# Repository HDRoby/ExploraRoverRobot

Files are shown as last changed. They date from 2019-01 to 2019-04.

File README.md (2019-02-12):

# Explora Rover Robot
6 wheels drive, all terrain, autonomous robot designed as a platform to experiment with autonomous driving vehicle.

Explora Robot is based on a well known commercial chassis widely available for hobbists 
[Dagu Thumper 6WD](https://www.sparkfun.com/products/11056).

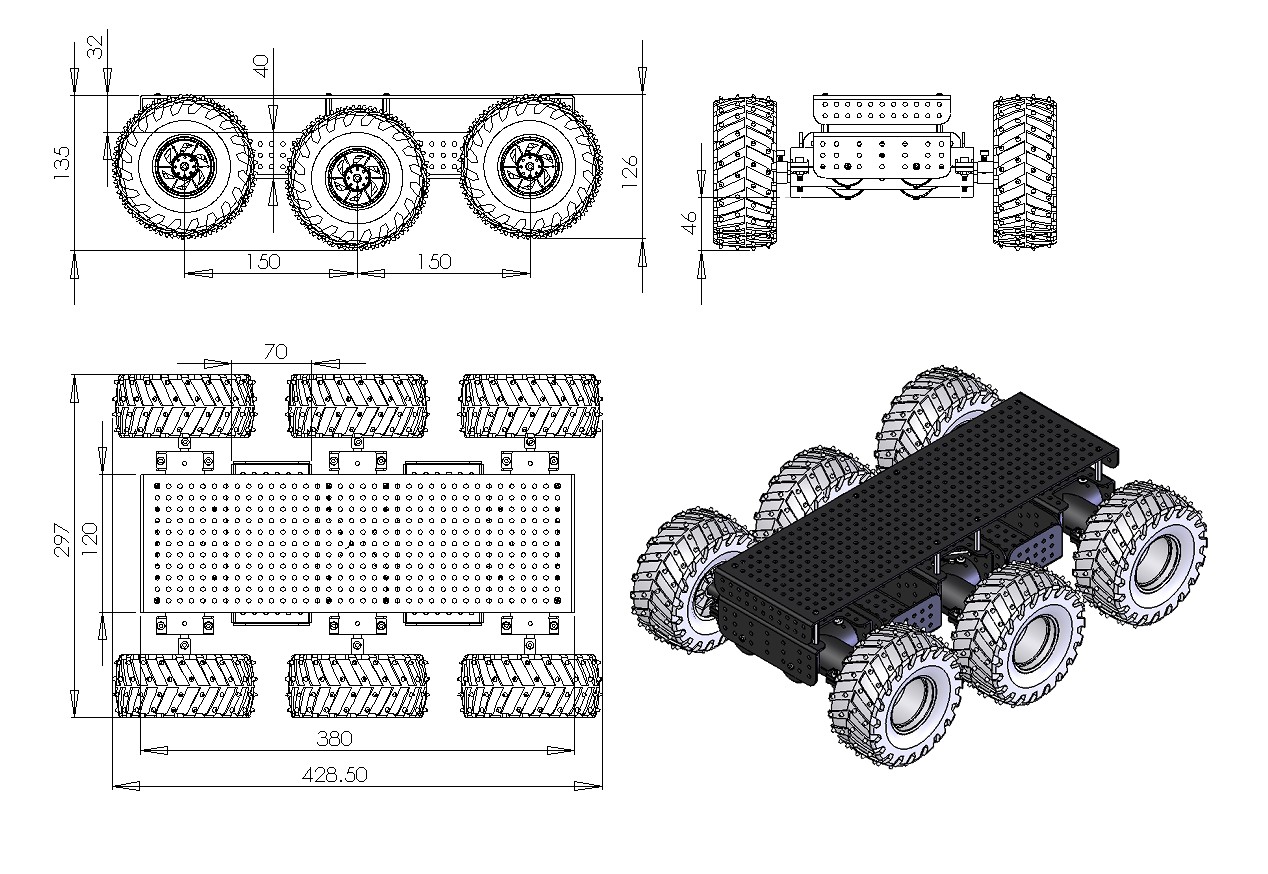
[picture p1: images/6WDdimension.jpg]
Dagu Thumper 6WD


Aim of this project is to design and build a robotic platform that will provide a set of interfaces, both software and hardware, that allow to build new layers with extended functionalities. Initial capabilities will include:

- indoor and outdoor navigation
- remote control and monitoring
- obstacle detection and avoidance
- simultaneus location and mapping (SLAM)
- viewpoints and landmark navigation
- terrain traversability estimation
- terrain negotiation
- path planning
- energy management and harvesting
- center of mass and pose estimation

## Tenets

- The system is open for modification without major disruption in all the parts.
- The robot can operate outdoor but its not designed for harsh environment. i.e. wet or dirty surfaces are allowed while waterproof is not in the scope.
- The energy consumption is frugal and a certain degree of autonomy is pursued. i.e. solar panel for energy harvesting or self recharging station could be implemented.
- The communication is bi-directional and mainly intended for monitoring and configuration than control (RC style).
- The robot can take advantage of many and concurrent localisation systems to establish its position in the environment. i.e. GPS, vision, LIDAR, utrasound, odometry, IMU, ...

## High level systems

Systems

### Power management system

This is responsible for providing power to the rover and all its subsystems, to monitor and recharge the batteries using both an external power source and solar panels. The system monitors the current drawn in real time by its major components: motors and all sub-systems; where possible each sub-system will provide its own power consumpion. Communications with the microcontroller (Arduino Micro) and other sub-systems is achieved via UART for the physical layer and with MQTT broker at ISO Application Layer (there will be a process on the main board (Raspberry Pi) that will have a process that act as a MQTT broker and that can communicate with a UART). 

Two mechanichal switches isolate the batteries from the rest of the system.

Power management system

### Motion control system

Motion control system

### Communication system

Communication system

### Logging system

The logging system is responsible for collecting data from each subsystem and storing it locally; the database of choice is InfluxDB (https://www.influxdata.com/time-series-platform/influxdb) that is a high-performance data store written specifically for time series data. The data we want lo log is in the format of time series and can be grouped in:
- **instrumentation data**. This is the data collected by the log system for each process that runs on every Raspberry PI. We use a logger that persists data on files, organised in folders with a specific naming convention (details in the paragraph). InfluxDB is installed on the main RPI and each other RPI has a process that periodically reads and import the log files into the DB, grouped by severity and by source and that takes care of their housekeeping.
- **system health data**. This collects all the data that allows to monitor and understand the system status. i.e. wifi RSSI, 2.4GHZ radio status, battery levels, system uptime, solar panes in use, number of remote sessions, number of battery recharges since day 1, etc.
- **sensors data**. This is the main source of data and is a collection of all the sensors, logged at the most appropriate rate. The only thing is not logged here, and probably is only stored in a folder, is the image video and audio (when capture is on) and image stills.

To complement the logging system, we will use Grafana  (https://grafana.com) to plot the data series collected.

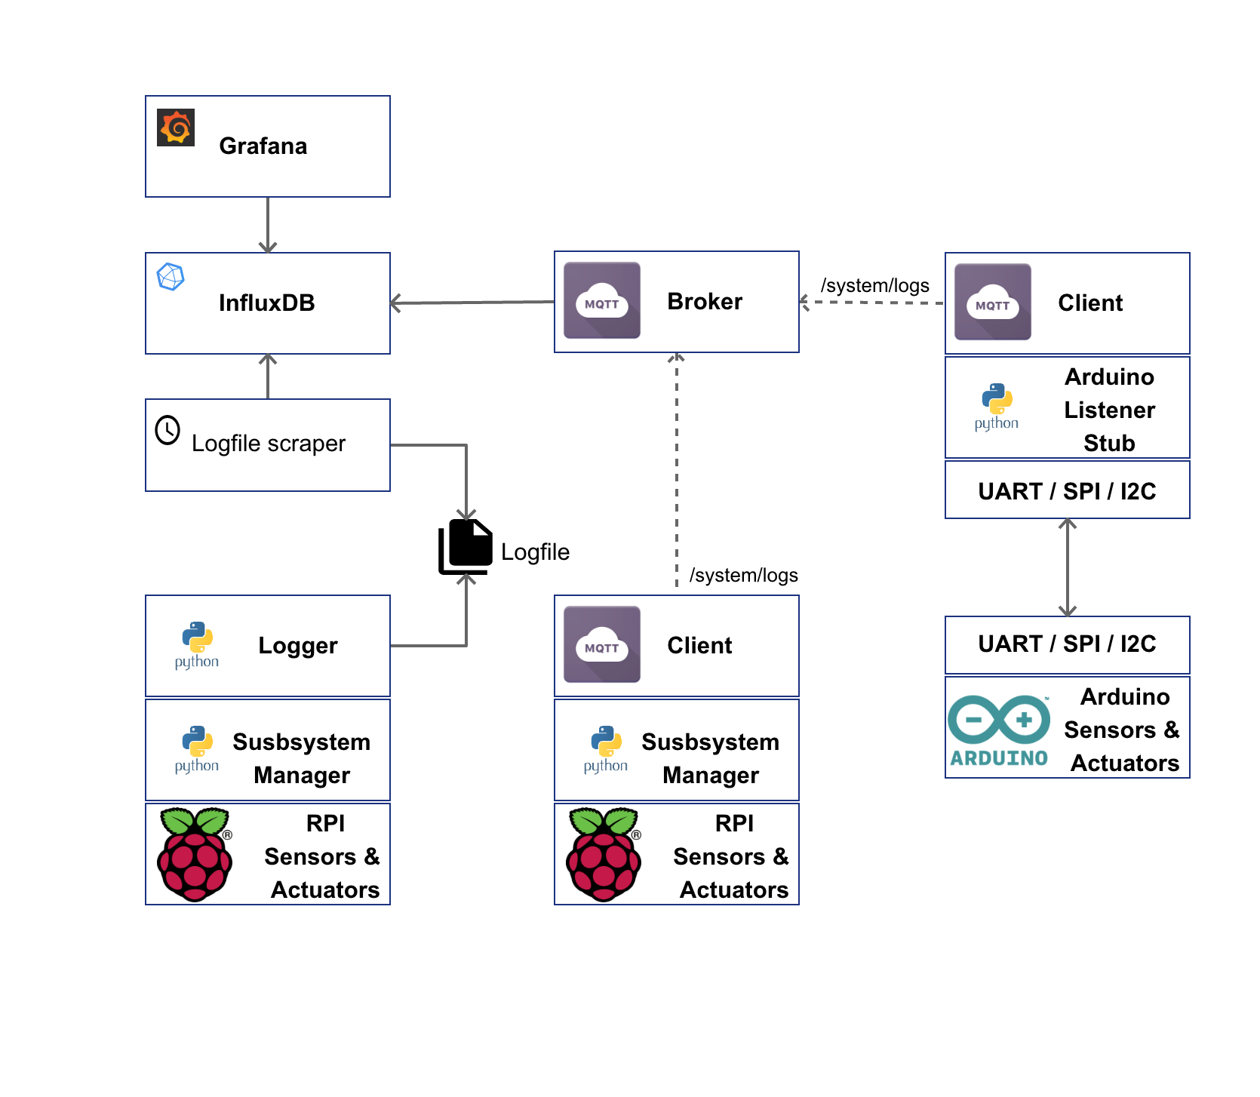
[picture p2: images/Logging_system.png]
Logging system


### Raspberry PI and Arduino systems
RPI is a much more powerful board than Arduino and the Linux OS simplify the management of the overall system, from the inter process communication (IPC) to the filesystem, wireless connectivity (WIFI & BTLE), multi process and multi threading. This is an overview of the architecture used to interact among a RPI and one or more Arduino. Note: in the robot there will be more than a single unit like this, that we consider as a basic processing unit (RPI + 1 or 2 Arduino) all RPIs are connected via Ethernet hub.

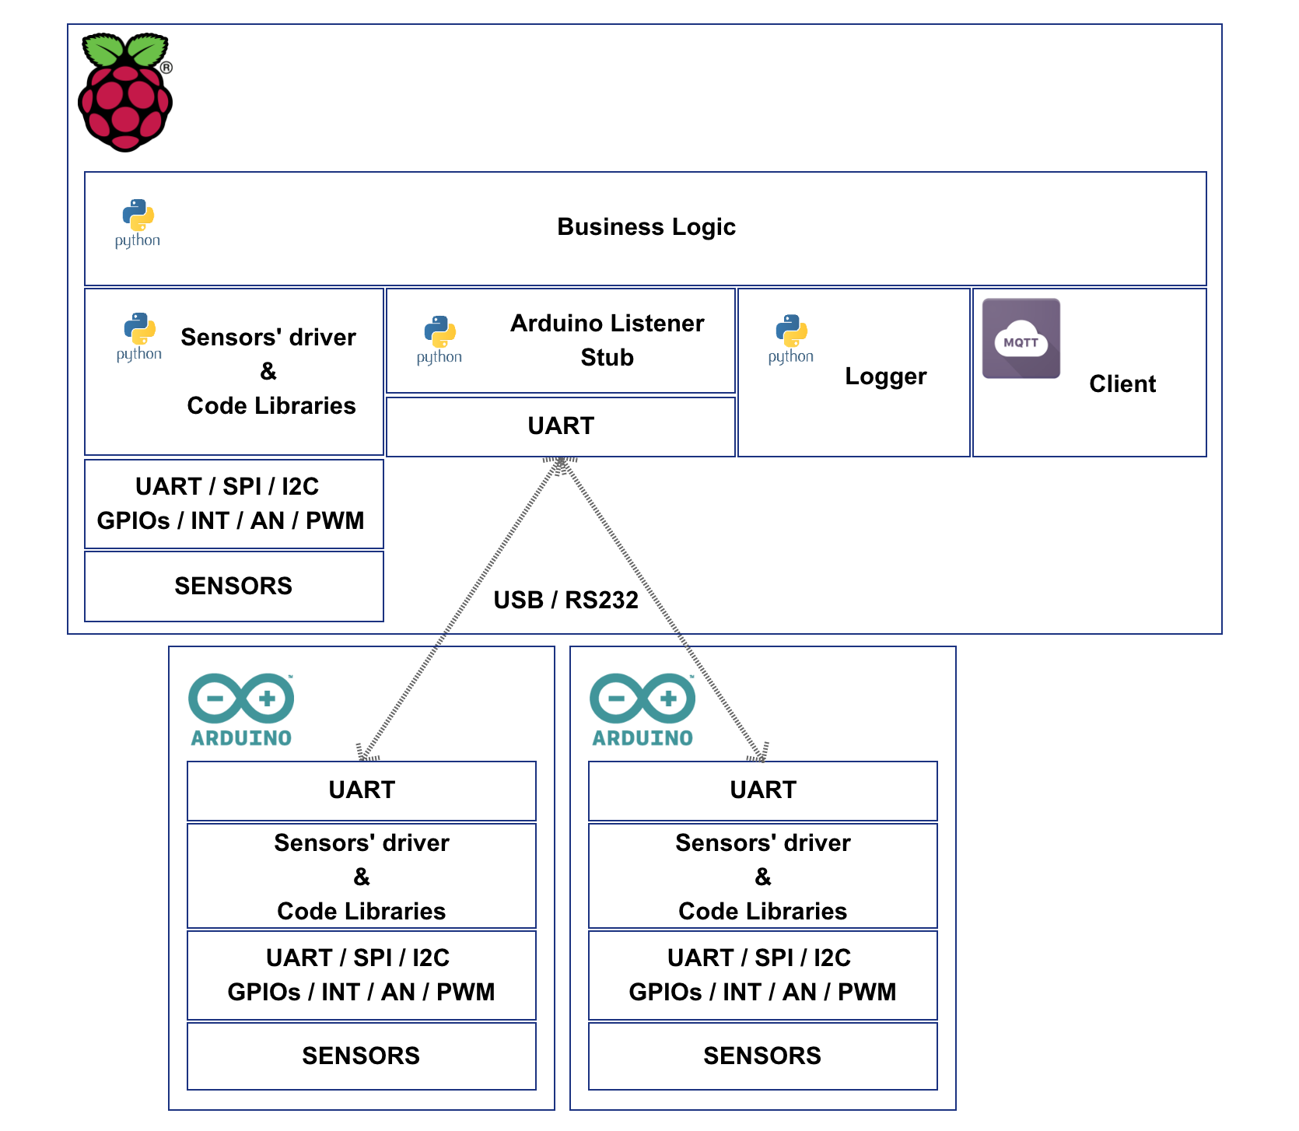
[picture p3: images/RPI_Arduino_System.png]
RPI Arduino system


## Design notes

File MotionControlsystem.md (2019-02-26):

# Motion Control System

We will use Dual H-Bridge Driver Motor Controller

## Features: 
Compact size, light weight.
Apply to control ordinary DC motor, smart car motor, etc.
Reversible control and PWM speed control.
Design of high-speed switch.
Ultra low internal resistance, low heat.

## Technical Specifications:
Operating Voltage: DC5V-12V
Standby Current: <30mA ± 5mA
Working Current: 0A-30A (Max) / each channel.
PWM mode: Duty cycle: 0-98%.
Frequency: General Motors: 16 kHz; Coreless Motor: 80 kHz; TEC: 500Hz-80kHz.
Input Voltage Level: Low: 0-0.5 V; High: 2.5 V-13 V (typical unit level: 3.3 V, 5 V, 12 V)
Current Sampling: CT Pin Output 

Voltage (V) = current (A) * 0.155

Item size: 6.2 x 5.3 x 1.8cm

## Pinout

1-6  | 7-12
---- | ----
CT_A | CT_B
EN_A | EN_B
IN1_A | IN1_B
IN2_A | IN2_B
GND | GND
V+  A | V+ B

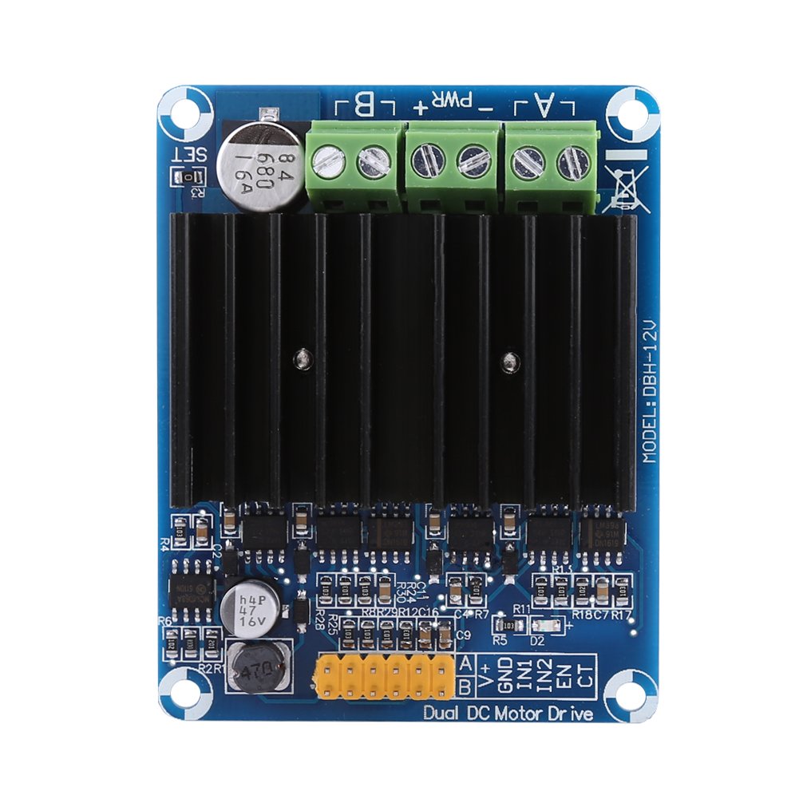
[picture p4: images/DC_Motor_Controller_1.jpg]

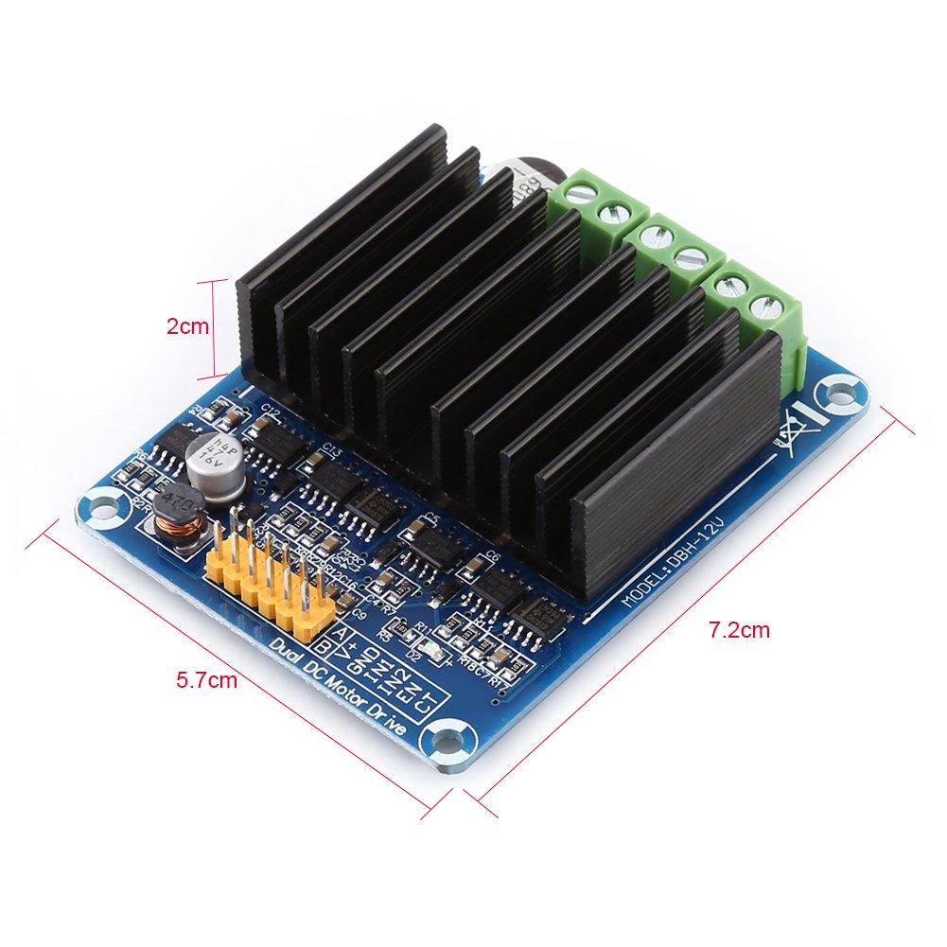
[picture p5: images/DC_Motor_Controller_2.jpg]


## Motor control protocol

### Low level communication

Commands sent to the controller:

to set the wheel diameter, used to compute the speed and to drive the robot using speed vector in the robot world:
```
[set_wheel_diam:120]

[set_pwm_range:|min:0|max:98]

[set_wheel_distance:250]
```

to set each motor speed:
```
[set_motors_speed|percent|left:30|right:-25]

[set_motors_speed|velocity|left:-120|right:-125]

[set_motors_speed|rpm|left:60|right:-60]
```

the sign indicate cw/ccw rotation

```
[set_motors_enable:true]

[set_motors_max_current:3500]

[set_motors_brake]
```

```
[set_robot_speed|radius:300|omega:-25.4]

[set_robot_speed|v_x:-300|v_y:254]
```

Values read from the controller:

```
[get_motors_status]

[side:left|enabled:true|rotation:cw|pwm:55|current:1540]

[side:right|enabled:true|rotation:ccw|pwm:15|current:420]
```

valid values:

  $I_{[mA]} =  \frac{1}{0.155} \times V_{[mV]}$

*note*: speed_rpm is after gear reduction

to compute the actual speed in [m/s], given the wheel diameter in [m]: 
$$ speed = \frac{\pi}{60} \times rpm \times d $$

# Inverse Kinematic

Standing in pose $(x,y,\theta)$ at time t, determine control parameters $v_l$ and $v_r$ such that the pose at time $t + \delta t$ is $(\dot{x},\dot{y},\dot{\theta})$.

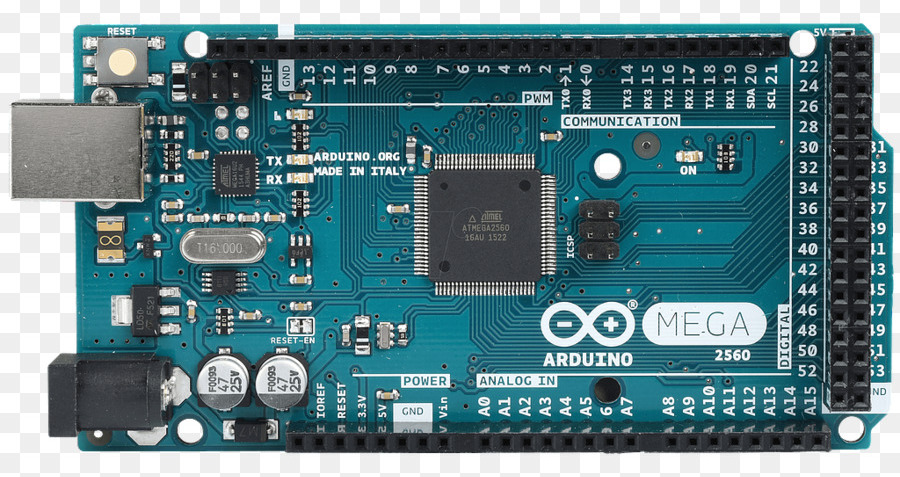
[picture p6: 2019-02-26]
images/arduino-mega-2560-pinout.jpg

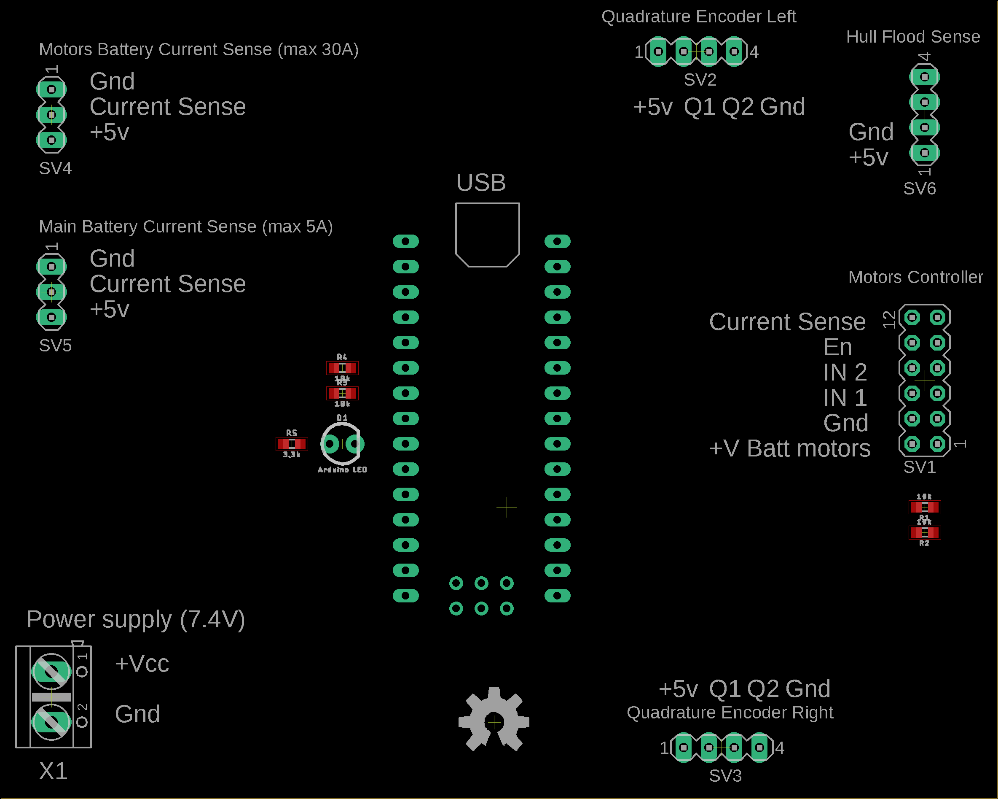
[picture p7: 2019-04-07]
Schematics/MotorsControllerSystem_Board.png

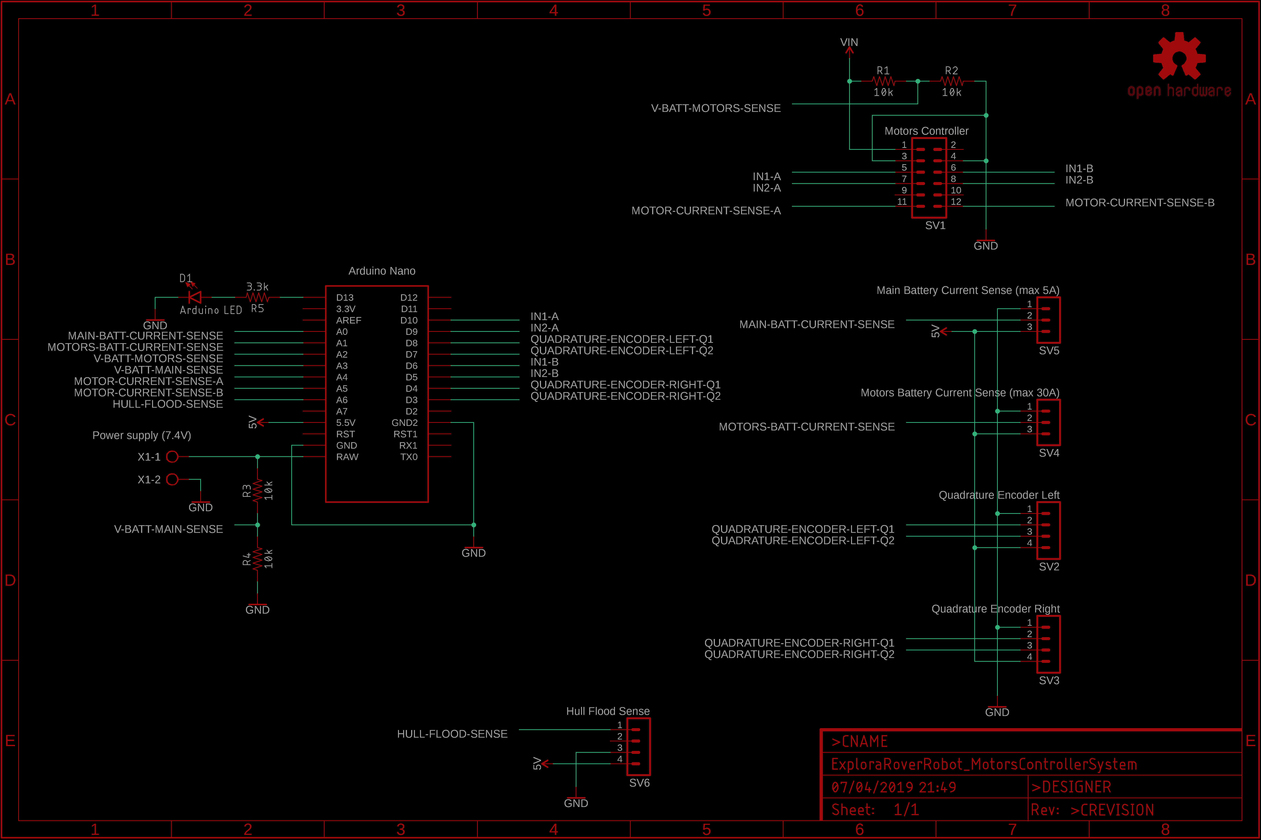
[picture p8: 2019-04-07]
Schematics/MotorsControllerSystem_Schematics.png

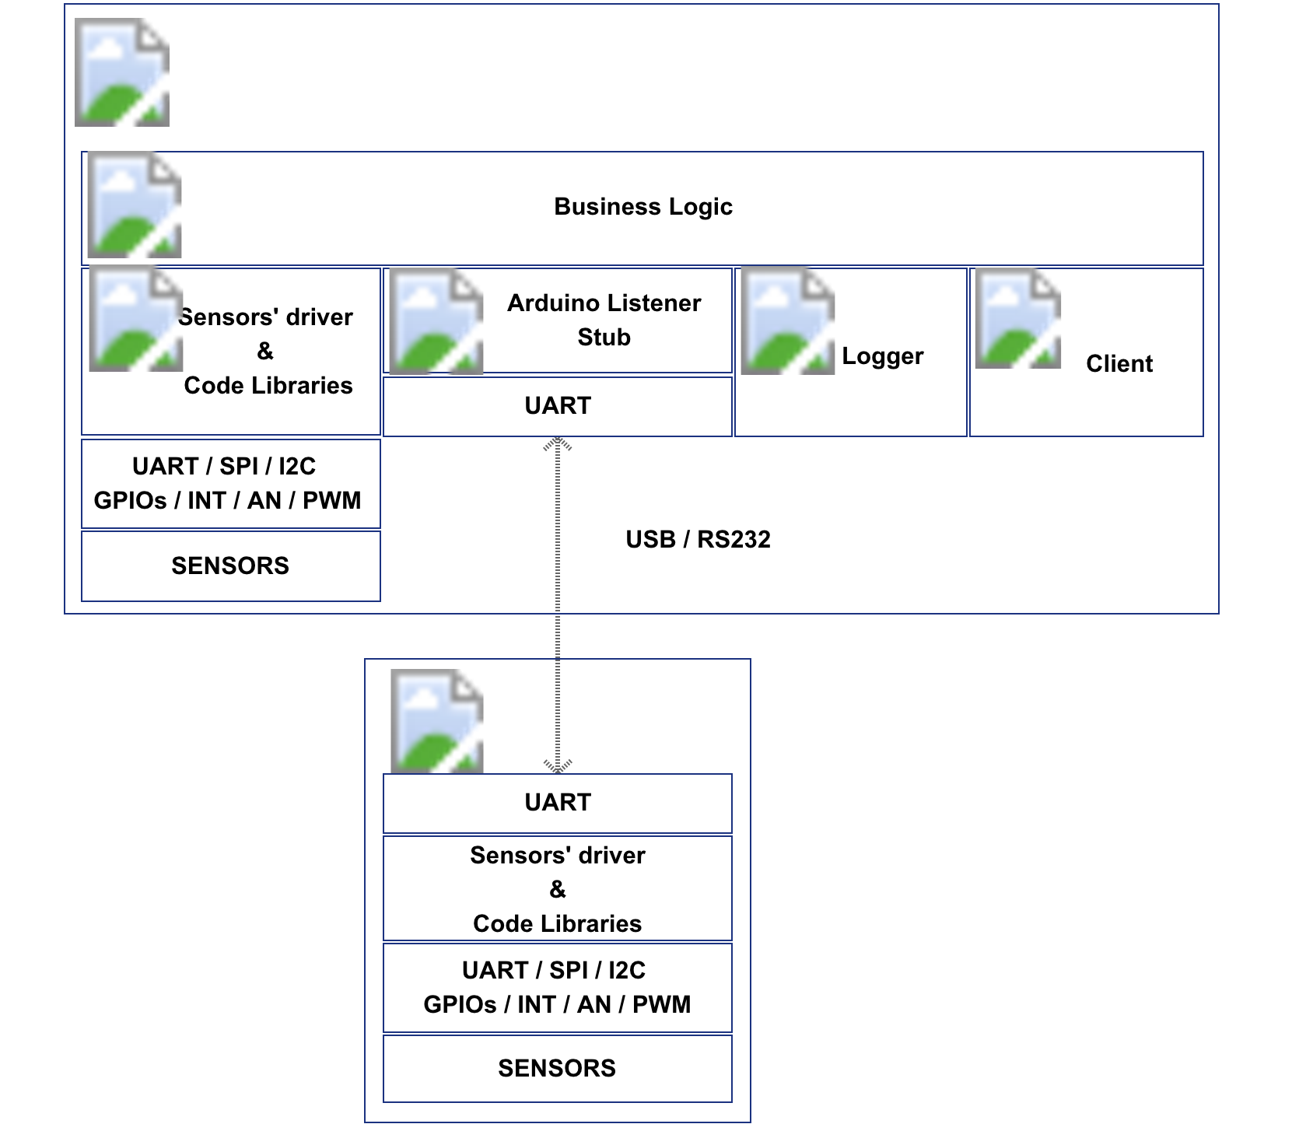
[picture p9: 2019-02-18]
images/untitled_page.png

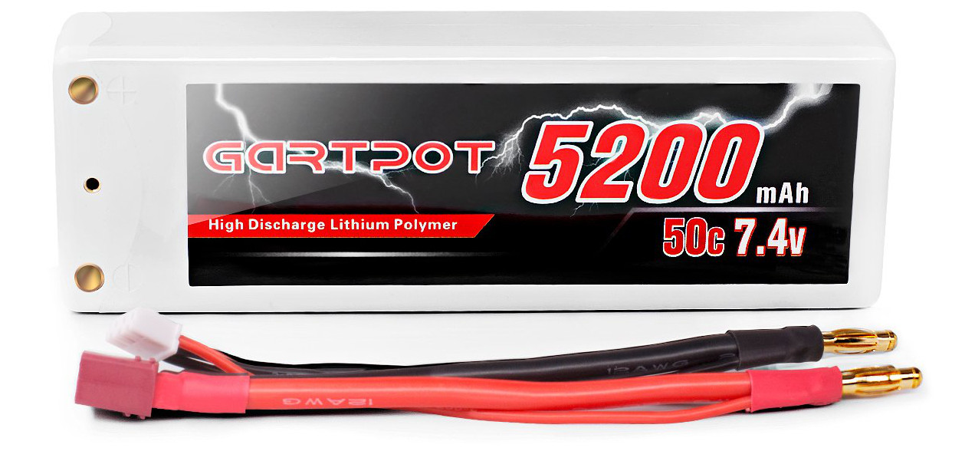
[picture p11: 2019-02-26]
images/Lipo Battery.jpg

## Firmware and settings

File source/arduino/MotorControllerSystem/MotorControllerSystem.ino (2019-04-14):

/*
 * Demo code to test the MotorControllerSystem and the libraries:
 * Battery, MotorController and QuadratureEncoder
 * 
 * Accepts input on the serial line and changes motor speed where [-1.0:1.0]
 * Prints a set of measures in json format using ArduinoJson library
 * 
 */


#include "MotorControllerDefines.h"
#include "Battery.h"
#include "MotorController.h"
#include "QuadratureEncoder.h"
#include "JsonSerializable.h"
#include "HullFloodSensor.h"
#include "SerialCommand.h"
#include <ArduinoJson.h>


#define BATTERY_DEBUG              
#define MOTOR_CONTROLLER_DEBUG              
#define HULL_FLOOD_DEBUG              
#define QUADRATURE_ENCODER_DEBUG              


Battery mainBattery(MAIN_BATT_V_SENSE_PIN, MAIN_BATT_I_SENSE_PIN);
Battery motorBattery(MOTORS_BATT_V_SENSE_PIN, MOTORS_BATT_I_SENSE_PIN);

MotorController motor_left(MOTOR_L_PWM_1_PIN, MOTOR_L_PWM_2_PIN, MOTOR_L_I_SENSE_PIN);
MotorController motor_right(MOTOR_R_PWM_1_PIN, MOTOR_R_PWM_2_PIN, MOTOR_R_I_SENSE_PIN);

QuadratureEncoder encoder_left(Q1_B, Q2_B);
QuadratureEncoder encoder_right(Q1_A, Q2_A);

HullFloodSensor floodSensor(HULL_FLOOD_SENSE_PIN);

SerialCommand commands;

void setup() {
  
  Serial.begin(9600); 

  commands.addCommand("speed",setMotorsSpeed);  
  commands.addCommand("stop",stopMotors);  

  motor_left.setAttribute("left");
  motor_right.setAttribute("right");
  
  mainBattery.setVoltageScaleFactor(2.0);
  mainBattery.setAttribute("main");
  
  motorBattery.setVoltageScaleFactor(2.0);
  motorBattery.setAttribute("motor");

  encoder_left.setupInterruptHandler(ISREncoderLeft);
  encoder_left.setAttribute("left");
  
  encoder_right.setupInterruptHandler(ISREncoderRight);
  encoder_right.setAttribute("right");

  floodSensor.setAttribute("bottom");

  stopMotors();
}

void loop() {
  commands.readSerial();    
  printJson();  
  delay(200);
}

void printJson()
{  
  serializeJson(motor_left.getJson(), Serial);
  Serial.println();

  serializeJson(motor_right.getJson(), Serial);
  Serial.println();

  serializeJson(mainBattery.getJson(), Serial);
  Serial.println();

  serializeJson(motorBattery.getJson(), Serial);
  Serial.println();

  serializeJson(encoder_left.getJson(), Serial);
  Serial.println();

  serializeJson(encoder_right.getJson(), Serial);
  Serial.println();
  
  serializeJson(floodSensor.getJson(), Serial);
  Serial.println();
}

void ISREncoderLeft()
{
  encoder_left.handleInterrupt();
}

void ISREncoderRight()
{
  encoder_right.handleInterrupt();
}

void setMotorsSpeed() {
  char *arg;
  
  arg = commands.next();
  if (arg != NULL) {    
     motor_left.setSpeed((float)atoi(arg)/100);    
  }
  arg = commands.next();
  if (arg != NULL) {    
     motor_right.setSpeed((float)atoi(arg)/100);    
  }
}

void stopMotors() {  
  motor_right.setSpeed(0);    
  motor_left.setSpeed(0);    
}

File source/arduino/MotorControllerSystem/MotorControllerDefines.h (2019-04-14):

#ifndef MotorControllerDefines_h
#define MotorControllerDefines_h


#define MAIN_BATT_I_SENSE_PIN       A0
#define MAIN_BATT_V_SENSE_PIN       A3

#define MOTORS_BATT_I_SENSE_PIN     A1
#define MOTORS_BATT_V_SENSE_PIN     A2

#define MOTOR_L_I_SENSE_PIN         A4
#define MOTOR_L_PWM_1_PIN           10
#define MOTOR_L_PWM_2_PIN           9

#define MOTOR_R_I_SENSE_PIN         A5
#define MOTOR_R_PWM_1_PIN           6
#define MOTOR_R_PWM_2_PIN           5

#define HULL_FLOOD_SENSE_PIN        A6

#define Q1_A                        8
#define Q2_A                        2
#define Q1_B                        4
#define Q2_B                        3

#define VFS                         5.0
#define VFS_HALF                    VFS / 2.0
#define ADC_RES                     1024.0
#define QUANTUM                     VFS / ADC_RES
#define ADC_TO_VOLT(adc) adc * QUANTUM 

// sensitivity expressed in mV/A
#define CURR_SENSITIVITY_30A        66  
#define CURR_SENSITIVITY_5A         185

#define LEFT                        0
#define RIGHT                       1


#endif

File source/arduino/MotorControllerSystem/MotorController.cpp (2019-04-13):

#include "Arduino.h"
#include "MotorController.h"

MotorController::MotorController(uint8_t pwm_1_pin, uint8_t pwm_2_pin, uint8_t i_sense_pin)
{
  _pwm_1_pin = pwm_1_pin;
  _pwm_2_pin = pwm_2_pin;
  _i_sense_pin = i_sense_pin;

  pinMode(_pwm_1_pin, OUTPUT);
  pinMode(_pwm_2_pin, OUTPUT);

  setSpeed(0);
}

void MotorController::setAttribute(String attribute)
{
  _attribute = attribute;
}

StaticJsonDocument<200> MotorController::getJson()
{
  StaticJsonDocument<200> doc = getBasicJsonDocument();
  
  doc["device"] = "motor";
  doc["speed"] = getSpeed();
  doc["current"] = getCurrent();

  return doc;
}

float MotorController::getCurrent()
{
  return ADC_TO_VOLT(analogRead(_i_sense_pin));
}

float MotorController::getSpeed()
{
  return _speed;
}

uint8_t MotorController::absSpeedToDutyCycle(float speed)
{
  return (uint8_t) (speed * (float)_max_duty_cycle);
}

void MotorController::setSpeed(float speed)
{
  _speed = speed;
  if (_speed < -1) _speed = -1.0; 
  if (_speed > 1) _speed = 1.0; 

  applySpeed();
}

void MotorController::applySpeed()
{
  uint8_t duty_cycle = absSpeedToDutyCycle(abs(_speed));

  if (_speed < 0)
  {
    analogWrite(_pwm_1_pin, duty_cycle);
    analogWrite(_pwm_2_pin, 0);
  }
  else 
  {
    analogWrite(_pwm_1_pin, 0);    
    analogWrite(_pwm_2_pin, duty_cycle);
  }
}

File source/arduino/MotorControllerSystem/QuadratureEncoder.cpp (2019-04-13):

#include "Arduino.h"
#include "QuadratureEncoder.h"
 
QuadratureEncoder::QuadratureEncoder(uint8_t q1_pin, uint8_t q2_interrupt_pin)
{
  _q1_pin = q1_pin;
  _q2_interrupt_pin = q2_interrupt_pin;

  _encoder_pos = 0;
  _new_position;
  _old_position = 0;
  _new_time;
  _old_time = 0;
  _attribute = "";
  
  pinMode(_q1_pin, INPUT);
  pinMode(_q1_pin, INPUT);
  digitalWrite(_q1_pin, INPUT_PULLUP);
  pinMode(_q2_interrupt_pin, INPUT);
  digitalWrite(_q2_interrupt_pin, INPUT_PULLUP);
}

StaticJsonDocument<200> QuadratureEncoder::getJson()
{
  StaticJsonDocument<200> doc = getBasicJsonDocument();
  
  doc["sensor"] = "q.encoder";
  doc["speed"] = getSpeed();  

  return doc;
}

void QuadratureEncoder::setupInterruptHandler(void (*ISR)(void))
{
  attachInterrupt(digitalPinToInterrupt(_q2_interrupt_pin), ISR, RISING);
}

float QuadratureEncoder::getSpeed()
{
  _new_position = _encoder_pos;
  _new_time = millis();
  
  float v = (float)(_new_position - _old_position) / (float)(_new_time - _old_time);  
  
  _old_position = _new_position;
  _old_time = _new_time;

  return v;
}

void QuadratureEncoder::handleInterrupt()
{
  if (digitalRead(_q1_pin) == digitalRead(_q2_interrupt_pin)) {
    _encoder_pos--;
  } else {
    _encoder_pos++;
  }
}

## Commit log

2019-02-04 update PowerManagementSystem block diagram
2019-02-05 Modify Power Supply System
2019-02-12 add RPI Arduino interaction
2019-02-18 add datasheets for lidar and motor controller
2019-04-07 Add schematics and layout for Motors Controller System
    [ExploraRoverRobot_MotorsControllerSystem.brd, ExploraRoverRobot_MotorsControllerSystem.sch]
2019-04-07 Add motors controller system block diagram
    [ExploraRoverRobot_MotorsControllerSystem.sch]
2019-04-12 add lidar and slam pdf to read
2019-04-13 add project Arduino Motors Contrller System with demo codefor libraries MotorController, Battey and Quadrature Encoder
2019-04-13 refactored code for the Motor Controller
2019-04-13 update to schematics and board for MotorControllerSystem
2019-04-14 change on the quadrature encoder pin to 2 and add schematics for Distance Sensors System
    [ExploraRoverRobot_DistanceSensorSystem.sch]
